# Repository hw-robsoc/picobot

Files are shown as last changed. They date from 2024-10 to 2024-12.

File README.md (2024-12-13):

# Welcome to the Robotics Society PicoBot Pico code

This repo contains the printable files for the Picobot, alongside the basic MicroPython code, which for Bluetooth control of the Pico's output pins, when connected correctly to the motor controller and servo. 

# Files

| |Description										|
|---|---|
|[main.py](https://github.com/hw-robsoc/picobot/blob/main/main.py "main.py")		|Main controller program, runs after boot of the Pico.|
|[test_motors.py](https://github.com/hw-robsoc/picobot/blob/main/test_motors.py "test_motors.py")|Test program to check that the directions of the motors are set correctly. |
|[test_servo.py](https://github.com/hw-robsoc/picobot/blob/main/test_servo.py "test_servo.py")|Test program to check that the directions of the servo are set correctly.|
|[RPI_PICO_W-20240602-v1.23.0.uf2](https://github.com/hw-robsoc/picobot/blob/main/RPI_PICO_W-20240602-v1.23.0.uf2 "RPI_PICO_W-20240602-v1.23.0.uf2")|The MicroPico firmware version we are using, which includes access to newer BLE libraries.|
|[PicoBot-AllDriveTypes.pdf](https://github.com/hw-robsoc/picobot/blob/main/PicoBot-AllDriveTypes.pdf "PicoBot-AllDriveTypes.pdf")|The laser cut design for all laser cut parts. Note: This is provided as a PDF, as when exporting to SVG from illustrator, the dimensions are wrong, and when exporting to DXF, the order of cuts is changed, resulting in parts that don't break away from the acrylic sheet.|
|[PicoBot-DrifterWheel.stl](https://github.com/hw-robsoc/picobot/blob/main/PicoBot-DrifterWheel.stl "PicoBot-DrifterWheel.stl")| 3D printable wheels for the drifer type kart.|
|[PicoBot-Pivot-Mount.stl](https://github.com/hw-robsoc/picobot/blob/main/PicoBot-Pivot-Mount.stl "PicoBot-Pivot-Mount.stl")| Sample pivot mount design for the racer type kart.|
|[Instructions-Session1.pdf](https://github.com/hw-robsoc/picobot/blob/main/Instructions-Session1.pdf "Instructions-Session1.pdf") [Instructions-Session2.pdf](https://github.com/hw-robsoc/picobot/blob/main/Instructions-Session2.pdf "Instructions-Session2.pdf") [Instructions-Session3.pdf](https://github.com/hw-robsoc/picobot/blob/main/Instructions-Session3.pdf "Instructions-Session3.pdf") [Instructions-Session4.pdf](https://github.com/hw-robsoc/picobot/blob/main/Instructions-Session4.pdf "Instructions-Session4.pdf")| Instruction sets for assembly, wiring, programming, and power system!|

# Flashing firmware to the Pico
Hold down the BOOTSEL button while plugging the board into USB. The uf2 file below should then be copied to the USB mass storage device that appears. Once programming of the new firmware is complete the device will automatically reset and be ready for use.
More information: https://micropython.org/download/RPI_PICO_W/

# Programming the Pico
We use [Visual Studio Code](https://code.visualstudio.com/) to program the Picos, along with the [MicroPico extension](https://marketplace.visualstudio.com/items?itemName=paulober.pico-w-go). Be sure to check the requirements of the extension, especially the requirements for a Python 3.10 or newer version to be installed on your PATH or equivalent.

Clone the repo to a projects folder, or download it via the green box above. Then, open the folder with VS code. If the MicroPico extension is already installed, it should automatically check your COM ports for a suitable device. When the device is plugged in, it will add a "Pico Connected" to your Status Bar, and give a notification that a connection has been made to the Pico. To upload your code to the Pico, press `CTRL` + `SHIFT` + `P`, or Mac/Linux equivalent, and search for `MicroPico: Upload project to Pico`. Select this option with `ENTER`, and wait for the code to be successfully uploaded to the device. 
For more information on how to use the MicroPico extension, see the [Marketplace Page](https://marketplace.visualstudio.com/items?itemName=paulober.pico-w-go).

# Brief code explanation
While some basic comments are included in the code, an overview can be found below:

- The [aioble](https://github.com/micropython/micropython-lib/blob/master/micropython/bluetooth/aioble/README.md) library is used to handle bluetooth connections, specifically Bluetooth Low Energy (BLE) connections. When combined with the tasks below, it is able to advertise, and receive payloads from other devices (your mobile phone running the Android app).
- The [asyncio](https://docs.micropython.org/en/latest/library/asyncio.html) library is used, which implements a subset of the standard CPython asyncio library. Three tasks are created to run concurrently in coroutines. These three tasks are:
	- **Blink Task** - This task simply checks whether a Bluetooth device is connected, and if it is, blinks the onboard Pico LED once every second. Otherwise, it blinks once every 1/4 second.
	- **Peripheral Task** - This task advertises the services and characteristics over BLE, and waits for a device to connect.
	- **Sensor Task** - This task waits for the chosen characteristic to be written to, and sets the motor control/servo control as required.
- There are then three additional functions.  `control_motors` processes the angle and strength of the joystick input, and converts that to motor speed and servo angle values. `set_motor_speeds` directly modifies the PWM output of each of the pins, according to the values calculated in the `control_motors` function. `set_servo_angle` directly sets the PWM output for the servo control, as per the value calculated again in the `control_motors` function.

## Batteries:  

Unfortunately due to the risk assessments we have, we are unable to give out the Li-ion batteries that were used to power the karts. However, if you are wishing to continue running/changing the kart over time, then you are more than welcome to buy your own batteries, but please be safe!

The exact cell that the society has are: Samsung 25R - 18650 Battery - 2500mAh - 20A, purchased from [CellSupply.co.uk](https://www.cellsupply.co.uk/samsung-25r-18650-battery). You do **not** need to get the exact cell, however having some of the same characteristics is key. I'll outline some of the characteristics below, then link to places to purchase them.

-   It should be an "18650" cell, which is simply the size of the cell (18mm diameter, by 65mm length) to fit in the holders on the karts.
-   It ideally should have a nominal capacity of around 2500mAh or higher.
-   It should have a nominal voltage of 3.6V (or 3.7V). The batteries we use are specifically INR chemistry, learn more about chemistry types [here](https://www.ufinebattery.com/blog/what-is-the-difference-between-imr-icr-inr-and-ifr-18650-battery/).
-   It should have a discharge rate of over 10A. The ones we use are 20A.

### Storage

Batteries themselves, when sitting at a sensible voltage (not too near either end of the extremes), and not fluctuating in temperature, are relatively safe. The main concern when storing them is to avoid shorting them against themselves or other batteries. This can be done using a case like the ones we had in the lab, or something like [this from Amazon](https://www.amazon.co.uk/JJC-Water-resistant-Batteries-Organizer-Carrying/dp/B08H511CPF).

### Charging

We handled charging the batteries between sessions using our own battery chargers, however, they can be charged using the BMS that is built into your robots. **Always monitor batteries when they are charging, never leave them unattended!**

Charging through a specific charger builds good practice for removing the batteries from the robot and storing them safely. Nu Batteries, as mentioned below, sells chargers suitable for Lithium Ion cells [here](https://www.nubattery.co.uk/chargers).

If you do wish to charge the robot through the integrated BMS, you will need to attach an input source to the P+ and P- pads on the back of the BMS. RobSoc has a number of USB-C charging ends that can do this, please reach out to us via email/discord if you want to do this, and I'll produce some instructions and tips! Otherwise, the BMS we use is listed in the instructions set on our [github](https://github.com/hw-robsoc/picobot).

### Buying

Like mentioned above, we bought ours in bulk from CellSupply, however, they can be bought from many sources. Buying them via Amazon for example will cost a large amount, and the quality/brand may be unknown or generic brands. Buying brands such as Samsung/Sony/Panasonic gives a little bit more piece of mind.

Alternatively, they can be bought in Vape shops, as the 18650 cells are often used in rechargeable vapes. You can usually get decent quality batteries in decent quality shops. None of our committee vape, however if you have a friend that does, asking them if they have bought batteries for their vape may be a good starting point to find a good quality shop.

We can only recommend CellSupply as we bought ours through them. They are however a wholeseller. They do have a sister site, Nu Battery, where you can buy the exact same cells in much lower qualities for a not too bad price increase. [Here is the same cells we use from NuBatteries](https://www.nubattery.co.uk/samsung-25r-18650-battery).

### Alternative chemistries:

I mentioned during the event that there may be alternative battery chemistries such as NiMH (nickle metal hydride) batteries, however I didn't know the nominal voltage off the top of my head. These batteries are safer, however, they have a nominal voltage of 1.2V, which means you would need a minimum of 4 of them vs the 2 we currently use. On the up side, that would possibly negate the need for the voltage converter (if you don't charge the cells fully). Without a redesign of the BMS/Voltage converter, you would **not** be able to directly swap in a NiMH battery, however if you are interested in doing this, please post on the Discord server, and we can try to figure it out!

## Finally, if you have any doubt, please send a message on our discord, and one of the committee would be more than happy to advise! Batteries when handled safely are a great resource!

# Licence

MIT License

Copyright (c) 2024 Bruce Wilson

Permission is hereby granted, free of charge, to any person obtaining a copy
of this software and associated documentation files (the "Software"), to deal
in the Software without restriction, including without limitation the rights
to use, copy, modify, merge, publish, distribute, sublicense, and/or sell
copies of the Software, and to permit persons to whom the Software is
furnished to do so, subject to the following conditions:

The above copyright notice and this permission notice shall be included in all
copies or substantial portions of the Software.

THE SOFTWARE IS PROVIDED "AS IS", WITHOUT WARRANTY OF ANY KIND, EXPRESS OR
IMPLIED, INCLUDING BUT NOT LIMITED TO THE WARRANTIES OF MERCHANTABILITY,
FITNESS FOR A PARTICULAR PURPOSE AND NONINFRINGEMENT. IN NO EVENT SHALL THE
AUTHORS OR COPYRIGHT HOLDERS BE LIABLE FOR ANY CLAIM, DAMAGES OR OTHER
LIABILITY, WHETHER IN AN ACTION OF CONTRACT, TORT OR OTHERWISE, ARISING FROM,
OUT OF OR IN CONNECTION WITH THE SOFTWARE OR THE USE OR OTHER DEALINGS IN THE
SOFTWARE.

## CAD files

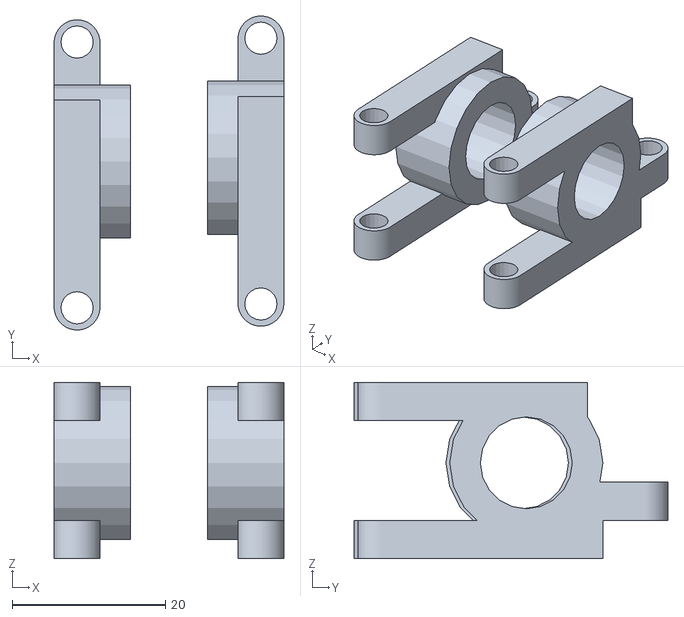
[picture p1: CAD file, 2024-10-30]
PicoBot-Pivot-Mount.stl
30.0 x 41.0 x 23.0

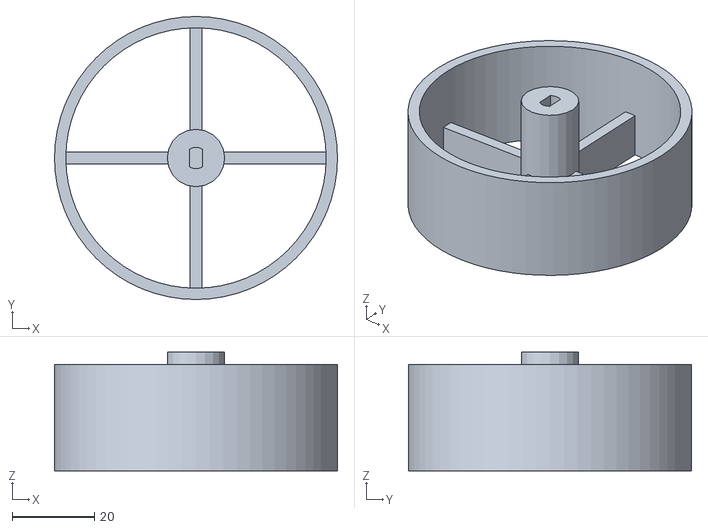
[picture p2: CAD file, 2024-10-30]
PicoBot-DrifterWheel.stl
69.0 x 69.0 x 29.0

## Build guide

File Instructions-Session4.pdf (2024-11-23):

# Robotics Society – Kart Workshop

### Session 4 – Power pack

Last week, we wired up and programmed the Pico for control from the Android app. This week, we will build and solder the power system, which works using a 2S Li-ion battery, with an attached BMS and step-down voltage converter. Both kart designs use the same power pack. Note: Lithium-Ion cells have very high power and energy density. Exercise common sense

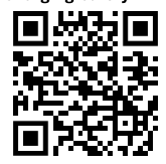
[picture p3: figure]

precautions when handling or testing.

# Part list

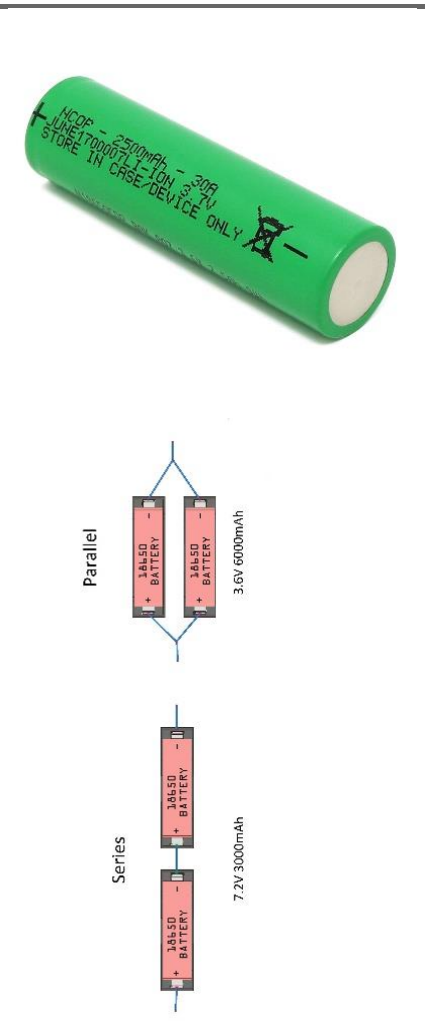
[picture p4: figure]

Part name | Description/use | Picture
Li-ion Battery Cell 18650 - 3.6V 2500mAh - 20A Information about Li-ion charging/safety: | We use these 2500mAh lithium ion cells to provide power to the system. Each cell nominally provides 3.6V, however, they can vary from 4.2V to 2.5V depending on their charge level. It is incredibly important to monitor their charge level, as keeping the voltage near either end of the range for a period of time can cause irreversible damage. Realistically, the voltage should never be allowed to drop below 3V. Even more dangerous is going past the end of this maximum/minimum, which can cause a fire or worse. Due to the variability of the voltage, firstly, a regulator is important to supply a constant voltage across the system. Secondly, a monitoring system is needed to keep within the range, as the batteries themselves do not monitor any of these factors.
| We will use two of these cells in series, and when batteries are placed in series, their voltage is added. Thus, we will have a nominal voltage of 7.2V, maximum of 8.4V, and minimum of 5V.

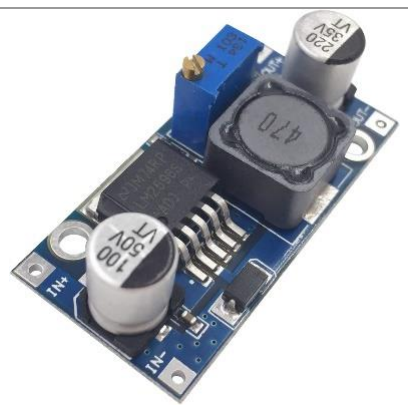
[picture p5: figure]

LM2596 DC to DC
Buck Converter

More about buck
converters:

As our nominal, minimum, and maximum vary significantly, we need to use a voltage regulator. If you remember from Session 2, the maximum voltage the RPi Pico can handle is around 5.5V.
We can use a step down buck converter to keep this voltage constant, around 5.2V. There are four solder pads on this board, two input, and two output, labelled by IN and OUT, and marked with a direction arrow on the back of the board.
We can adjust the voltage output by taking a screwdriver and turning the brass screw in the blue variable resistor. Test the output by attaching a voltmeter to the OUT pins, and vary the position of the brass screw to see its output.
2S 3A Li-ion Battery
Charger Protection
BMS

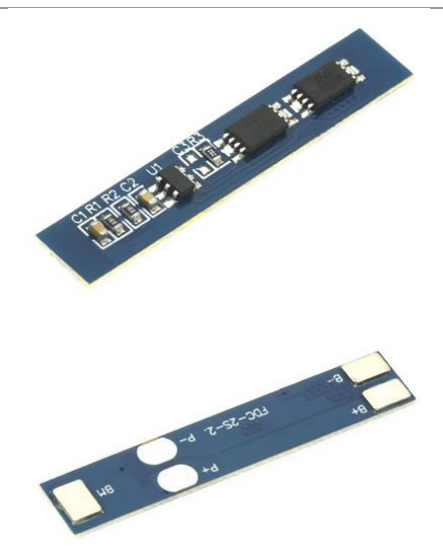
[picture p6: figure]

As mentioned above, ensuring that the li-ion battery is not over-discharged, over-charged, or too much current is drawn from the battery, we use a BMS, which stands for Battery Management System. This small chip takes three input, B+, B-, and BM. B+ and B- are simply the positive and negative input from the battery itself. BM however connects to the midpoint between the two batteries, which ensures that both batteries are charged at the same rate, and individual cells can have their voltage measured. P+ and P- are then multiuse pins, acting both as charging pads and discharging pads. For our basic use, we will connect the P+ and P- pads to just discharge, and charge the batteries using a Li-ion charger. However, USB-C connectors are available to solder on if desired.

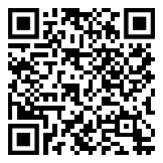
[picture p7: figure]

# Wiring Diagram and Description

Ideally, the cells would be contained within a small housing, with the BMS and voltage regulator attached to the outside, however, as we are placing the cells into a cell holder anyway, the outside of this can be used to attach the components to.

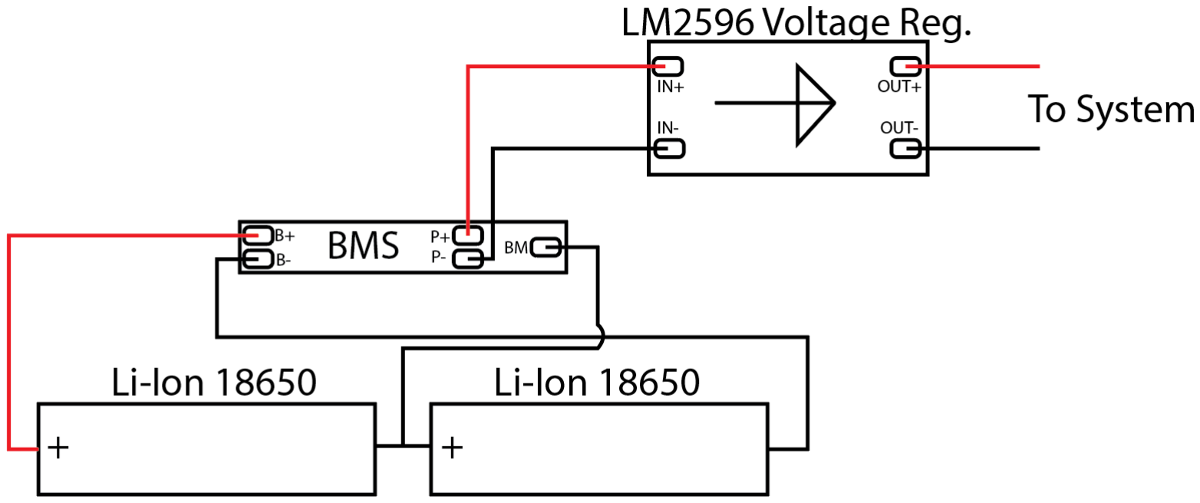
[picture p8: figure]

The diagram above demonstrates the principles covered in the part list in action. The BMS can be mounted to the side of the battery holder, where as the voltage regulator can be mounted atop the batteries themselves with a piece of tape.
Key to this part of the project will be soldering. DO NOT solder directly to a li-ion battery, it is highly dangerous, and even the prolonged high temperature can damage the cells. In this workshop, we are using a 2x18650 plastic holder, however in practice, many cells are joined together using spot welding and nickel plating.
A few notes to take into account, the pads on the BMS like to move about when the solder flows, so a steady hand is needed to keep them in place, and leave them to cool once in position. Additionally, soldering the connector piece for the BM lead is tricky, and has to be soldered onto a connector on the battery pack itself.
In the session, we will take small groups over to solder these together, but outside these sessions, please do let us know if any help is required.
Please note, we require the cells back at the end of the session, or for them to be stored securely between sessions. Leaving exposed cells around can be dangerous, especially if someone without the knowledge of the cells starts handling them.

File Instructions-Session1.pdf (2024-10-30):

# Robotics Society – Kart Workshop

### Session 1 – Assembly

Welcome to the Robotics Society Kart Workshop! Over the
course of 3-4 weeks, you will be assembling, wiring up, soldering, and powering your very own kart, which can drive around our track, and compete in our competition on November 20th

,
hosted in the National Robotarium!
These instructions are intended to be followed alongside the
practical workshop, with RobSoc committee guiding you through
each instruction – however they are also produced for those who

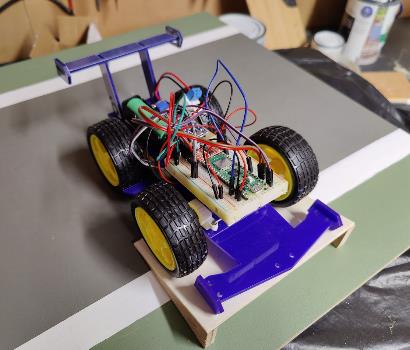
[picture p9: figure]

cannot make the sessions, or want to catch up. Please let us know if anything is not clear! Following the instructions throughout the sessions will get you a working kart – however it will not be the best you can make! The general kart we designed was built for ease of manufacturing and simplicity, at the cost of speed and control. Thus, it is up to you to make changes and make your kart the fastest round our course!

# Your choices – Racer or Drifter

First, there are two base designs for the kart, the “racer” and the “drifter”, with subtle changes to the assembly and wiring depending on which design you choose. The racer style makes use of four rubber wheels, rear-wheel drive with two motors, and a servo at the to pivot the front wheels to steer. The drifter style makes use of differential trust steering on the front two rubber wheels, and free spinning 3d printed wheels at the rear to reduce friction.
Both kart designs use the same laser cut components, and a majority of the holes and mounting points on the laser cut parts are not used, but are there for mounting any powerups you wish to add, or modifying your kart design without using the laser cutter.

# Assembly Steps

We’ll start with basic assembly which applies to both karts, then break off into specific assembly relevant to each kart design.
A huge note: Our budget is tight, especially with us not charging membership this year. Cheap acrylic was bought, which has quite a large variation of depth across its surface. Thus, parts can be tighter/looser than intended in the design. A sheet of sandpaper and a needle file can go a huge way, and parts such as the vertical connectors or spoiler are prone to breakage. Don’t worry if a part snaps! We have made many spares to account for the variation.
Additionally, various inserts may be stuck inside other pieces – just give them a gentle push with a fingernail or tool and they should pop out.

## Laser Cut Parts

The below kit will be provided, with other parts – not including electronics – are provided either through the society box or the GRID tower (for bolts and wires). See the other parts list below for a full description

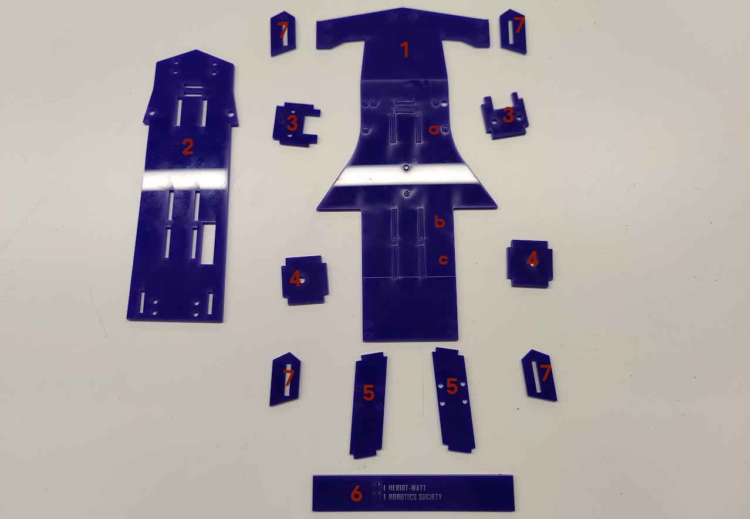
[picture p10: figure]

## Additional Part List

Racer | Drifter
- 4x rubber yellow wheels • 1x sg90 micro servo • 1x half servo horn with 3mm hole drilled at 3rd up • 2x yellow motor (double shaft) with crimped connectors • 2x 3d printed pivot wheel mounts • 2x 12mm 4mm bore shaft bearings • 4x 4mm shaft collars • 2x 4mm 26mm aluminium axle • 1x 2mm steel wire control linkage • 2x M4*16mm bolts (with 4x M4 nuts) • 4x M3*25mm bolts (with 4x M3 nuts) • 1x breadboard | • 2x rubber yellow wheels • 2x 3d printed wheels • 1x 4mm 83mm aluminium axle • 2x yellow motor (double shaft) with crimped connectors • 4x M3*25mm bolts (with 4x M3 nuts) • 2x 4mm shaft collar • 1x breadboard

## Part Descriptions (for reference)

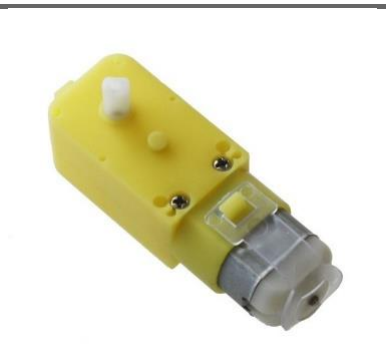
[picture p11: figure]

Part Name | Description/use | Picture
Yellow Motor with crimped connectors | These motors are relatively slow, but with the gearbox addon can produce a reasonable amount of torque. Expect around 90RPM from their output, when given nominal voltage of 4.5V (operating range of 3V to 6V). Motors rotate when a voltage is applied across them, and while modifying their speed via adjusting the voltage is possible, it is far better to modify their speed using PWM signals, and we go a step further by using a motor controller, which will be explained in session 2.

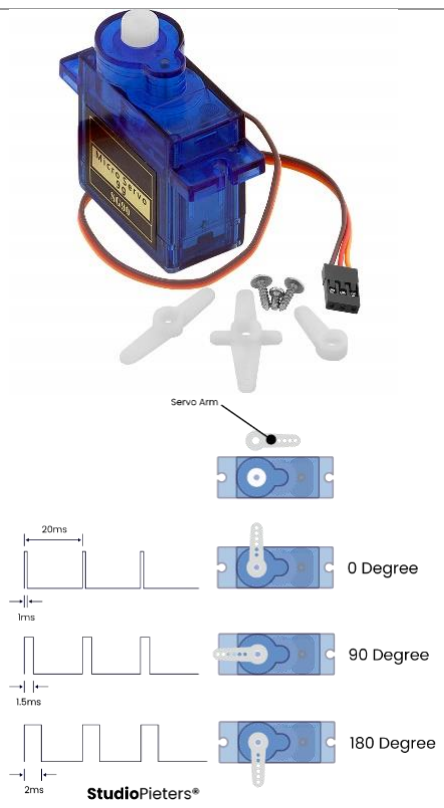
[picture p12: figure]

SG90 Micro
Servo / Half
servo horn

Learn more
about servos
and PWM:

Servos require both a supply through their red and brown wires, but also a signal through the yellow wire. This signal is a PWM signal, which stands for Pulse Width Modulation. By applying short pulses of voltage in a specified pattern, the servo can be made to rotate to and hold a certain angle, which in our case, is between 0 and 180 degrees. In the example to the right, it is shown how adjusting the length of the pulse while keeping signal frequency (50 Hz) the same, can rotate the servo between 0 and 180 degrees.
The servo horn is the small piece of plastic that attaches to the end of the gear train, and can attach to your control linkage to pivot the wheels at the front of the racer kart. This piece is incredibly easy to snap – which is beneficial if the servo tries to rotate too quickly, and you’d rather the horn snapped than the servo broke itself.
The SG90’s that we are using can safely handle up to about 5.3V, and will probably not rotate with anything under 3.3V. Servos can be current hungry when they rotate quickly and with load, easily spiking to 2A. This is the reason a 2S system with step down voltage will be used for the power system.

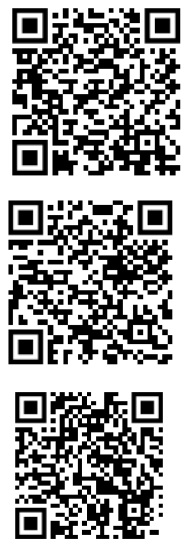
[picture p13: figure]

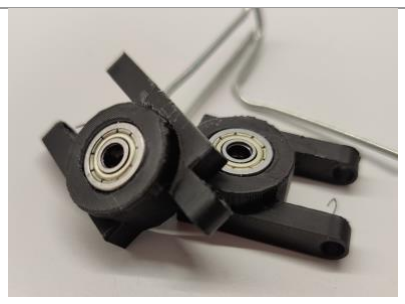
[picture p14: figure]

3D printed Pivot wheel mounts | These parts are designed to hold a bearing, and connect to both the top and bottom assembly of your kart. They are not optimal, as they rotate about 20mm off the axle connection point. An improvement to your robot could easily be designing a 3D printed piece that connects directly below the axle connection point (hint: there is a pre-made hole in part 1 where this could go!)

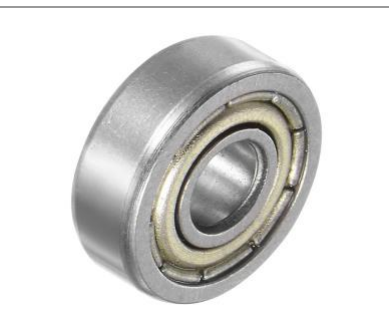
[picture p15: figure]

Shaft bearings | These bearings allow for the front wheels of the racer type kart to rotate easily and with less friction. They have an external diameter of 12mm, and an internal bore of 4mm, which fits the aluminium axle. Hint: These could be used on the drifter type cart to allow both rear wheels to spin independently, which would reduce friction further, rather than having both rear wheels mounted on the same axle.

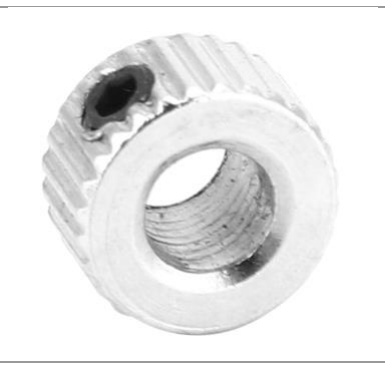
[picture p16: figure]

Shaft collars | Shaft collars prevent the axle from slipping around, and are tightened using an M3 grub screw. The inner bore of the shaft is 4.1mm.
Aluminium Axle | The drifter kart design uses a single axle at the rear connecting both wheels together, using shaft collars to prevent slippage. The racer kart design uses two axles at the front to connect the wheels to the bearing mounted inside the pivot wheel mount. The aluminium is 4mm round bar, which is relatively easy to bend or grind, with all squared ends done using a bench sander.

## Step 1

Start by assembling the spoiler and top assembly to get an idea of how the parts fit together, and how much sanding is needed. Part 5 (spoiler bars) will slot into part 6 (spoiler), such that the logo is facing up, and the spoiler bars are both heading the same direction. Both part 5’s should then assemble together into part 2 (top plate), and form the image you can see on the right. Part 7 can be added as
desired to the sides of the spoiler.

## Step 2

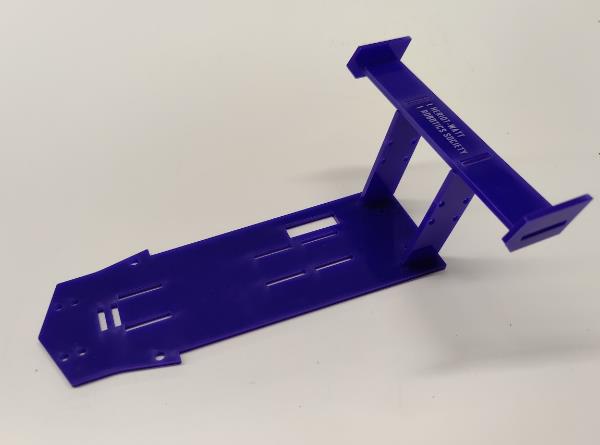
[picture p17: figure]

Each yellow motor should be connected to part 3, with the mouth of the space invader facing towards the silver end of the motor, and with the copper solder points of the motor facing towards part 3 as shown. Two 25mm M3 bolts should be inserted through the motor and through part 3, and two M3 nuts placed on the end to hold the piece together, as shown on the right.

## Step 3

Depending on the kit you receive, you may receive motors

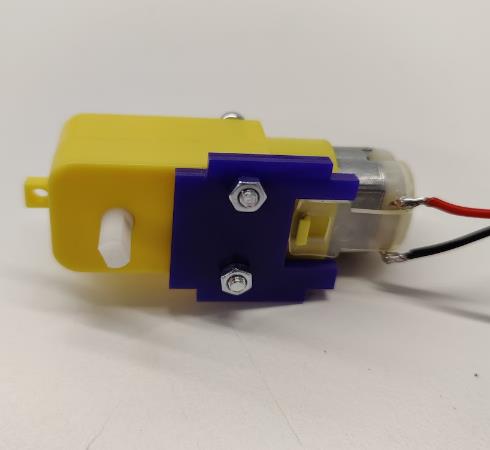
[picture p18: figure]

with pre-soldered connectors, or just copper tabs on the end of the motors. If you have never soldered before, please come along to one of our sessions, and we can teach the basics of how to solder onto these tabs. If you know how to solder already, feel free to solder wires of around 15cm length onto these tabs, multicore, with a max AWG of 16 (to enable easier crimping). Once the motor wires are soldered, 2x1 crimps should be added to the end, to aid with connection to the breadboard (RobSoc has crimping tools in the box, or, there should be a crimping tool and crimps per floor of GRID).

## Racer Steps

### Step 4

Insert the two motors mounted on part 3 in the rear straight holes of part 1 (labelled b in the diagram of laser cut parts). The end of the motors, with the yellow piece of plastic sticking out, should align with the engraved line on part 1, as shown to the right. Both part 4’s can then be inserted into the front straight holes on part 1 (labelled a in the diagram of laser cut parts). Once this bottom assembly is together, you can test fit whether the top assembly that you made in part one fits, or requires further sanding of parts 3 and 4. Then, attach two rubber wheels to the motors at the rear.

### Step 5

Two 3d printed pivot wheel mounts either in black or white will be included with the kit. Press fit one 12mm bearing into each pivot mount, with the bearing flush with the protruding section of the mount, as shown to
the right. Next, these mounts should be
attached to part 1 with a 16mm M4 bolt, with

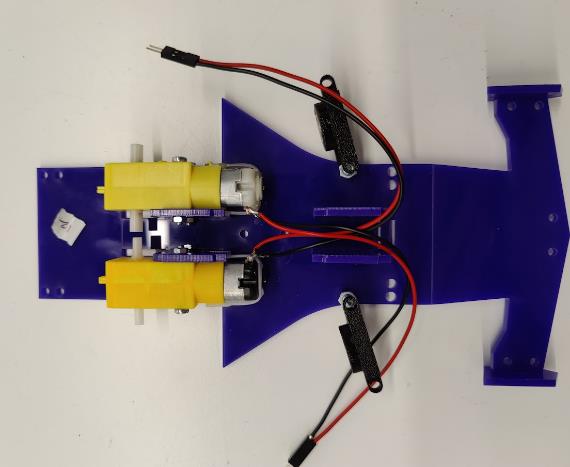
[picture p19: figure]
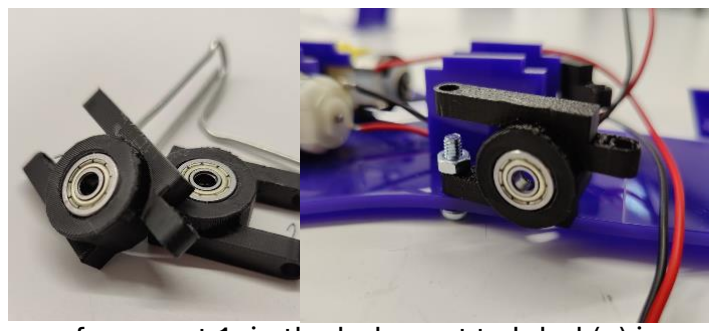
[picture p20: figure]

the protruding piece of the pivot mount facing away from part 1, in the hole next to label (a) in the laser cut parts diagram, and secured with a single M4 nut. Once you are happy with the positioning, a second M4 nut can be used to tighten the two nuts against one another, preventing vertical movement of the pivot mount, but allowing rotation.

## Step 6

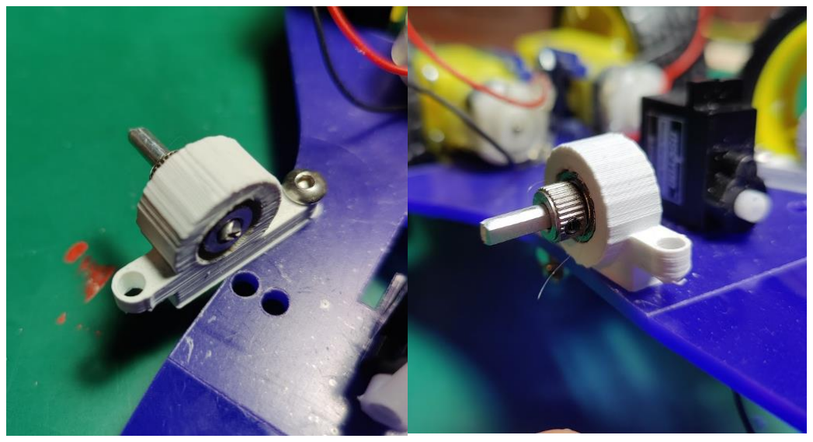
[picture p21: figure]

Position one 26mm
axle through each of
the bearings, such
that the chamfered
end is facing away
from part 1. On each
axle, place a shaft
collar either side of
the bearing, and
tighten the grub nuts
so that the axle
extends no further
past the end of the
shaft collar.

## Step 7

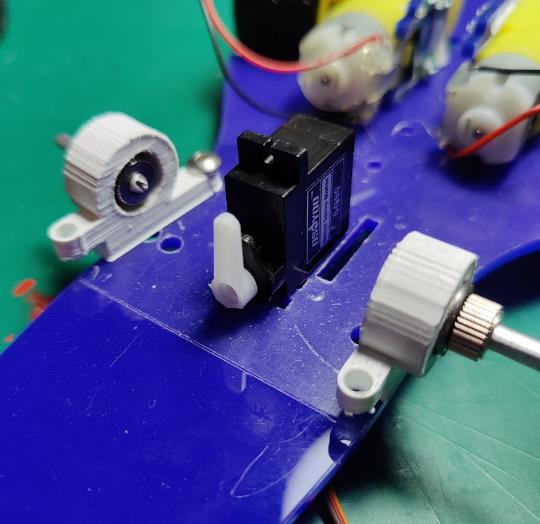
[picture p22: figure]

Mount the servo with the single armed horn (white piece that attaches to the rotating circle on the servo) in the centre straight holes of part 1. There are two position options, depending on how you design the control linkage in step 8, and we recommend the rear option. A key note: is that the servo may have been rotated prior to mounting, and you cannot guarantee that the position you put the horn will be the centre of the servo. Thus, always ensure in your design that you can remove the servo horn from the servo itself.

## Step 8

Connect the servo to either pivot rod ends using a control arm, made from steel wire. This design can take many forms, with benefits and drawbacks to each, and is a key point where upgrades can be made to the kart, for example, using multiple moving components to implement Ackerman steering. The example shown to the right creates a relatively large turning circle, and by changing the attachment point on the servo horn, a smaller circle is possible, by
increasing the pivot range.
Some additional details: You want the wire to be

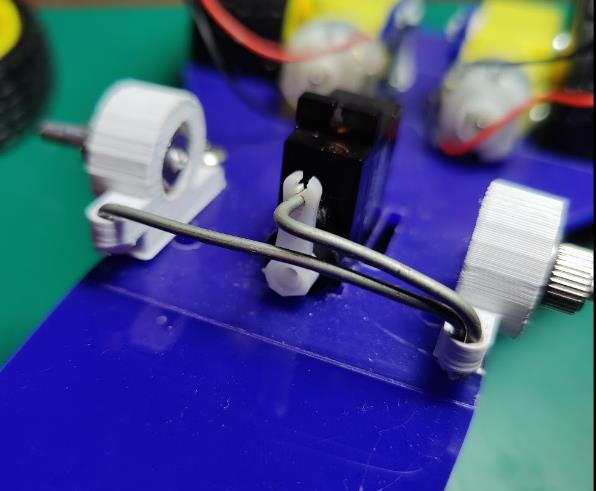
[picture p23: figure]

able to rotate within each of the pivot rod ends, and rotate within the servo horn itself. The servo horn will also need drilled out to 2mm if using the steel wire supplied, which is best done very slowly, and using just friction and a bit of force, though, don’t worry if it snaps at the end, this is usually okay, unless it snaps closer to the horn connector.

## Step 9

Attach the top assembly onto the bottom assembly, and mount two rubber wheels onto the ends of the 26mm axles. If they are loose, they can be secured by hot gluing a small blob onto the wheel hole, then inserting the axle and letting the glue set. Attach part 7 to the front of part 1 and sides of part 6 as desired, then assembly of the racer type kart is complete! Next steps are beginning wiring and electronics, covered in session 2.

## Drifter Steps

### Step 4

Insert the two motors mounted on part 3 in the front two straight holes of part 1 (labelled a in the diagram of laser cut parts). The end of the motors, with the yellow piece of plastic sticking out, should aligned with the engraved line on part 1, as shown to the right. Both part 4’s can then be inserted into the rear straight holes on part 1 (labelled c in the diagram of laser cut parts). These should be inserted with the centre hole higher, otherwise the kart will be unbalanced. Once this bottom assembly is together, you can test fit whether the top assembly that you made in part one fits, or requires further sanding of parts 3 and 4.

### Step 5

Insert the supplied 4mm*84mm axle through the two holes in part 4. Then center and secure it using two 4mm bore shaft collars, by tightening the black grub screws in the collar. Then, attach the two 3d printed wheels to the ends of the axle. If they are loose, they can be secured by hot gluing a small blob onto the wheel hole, then inserting the axle and letting the glue set.

## Step 6

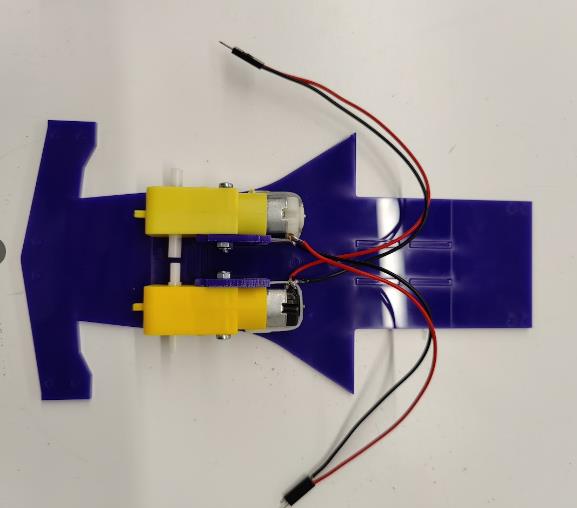
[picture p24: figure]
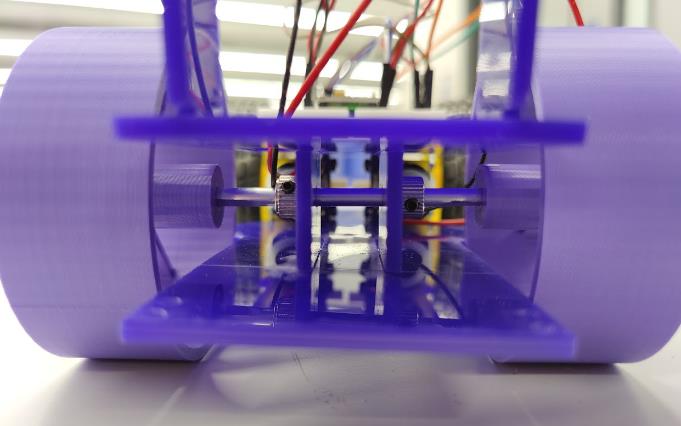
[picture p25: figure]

Attach the supplied rubber wheels to the motors at the front of your kart, and part 7 to the front of part 1 and sides of part 6 as desired, then assembly of the drifter type kart is complete! Next steps are beginning wiring and electronics, covered in session 2.

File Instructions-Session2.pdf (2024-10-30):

# Robotics Society – Kart Workshop

### Session 2 – Electronics

Last week, you began assembly of the karts, putting together the laser cut frame and beginning the wheel assemblies depending on your design. Today we will be completing the initial electronics setup, wiring up the Raspberry Pi Pico, DRV8833 motor controller, and depending on your choice of kart, the wheels or servo. We don’t include a direct wiring diagram in here – that’d be too easy! But you can compare against the working kart in the sessions.

# Part list

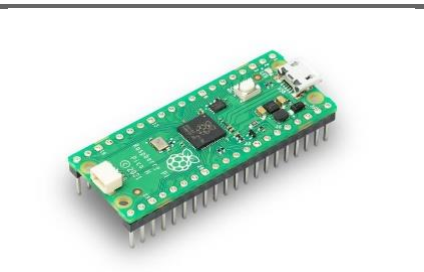
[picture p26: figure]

Part name | Description/use | Picture
Raspberry Pi Pico W Documentation: | The main controller for the system, receiving input from its onboard Bluetooth chip, processing the input signals, and outputting appropriate PWM signals to the motor controller. The Pico itself can handle an input voltage of up to around 5.5V, though we recommend keeping it slightly below this. The whole board can be programmed in multiple languages, for our workshop we will be using MicroPython. Though it can be programmed directly in C, the software that interfaces with the Bluetooth capabilities is much more complex in C than Micropython.

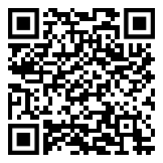
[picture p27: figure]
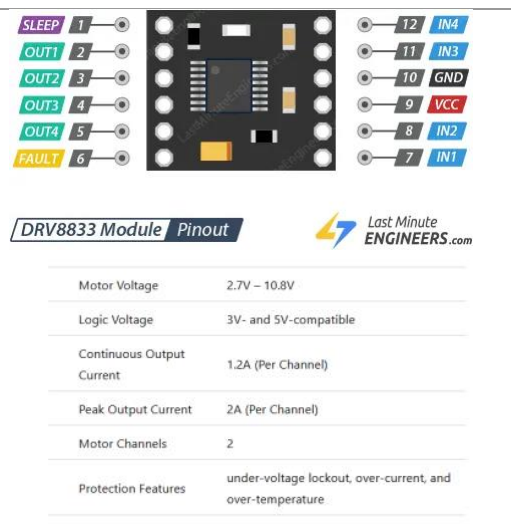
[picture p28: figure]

DRV8833 Motor Controller Documentation: | This board receives the PWM signals from the Pico and controls the motor forward and backwards at varying speeds. Using a motor controller is important, as the Pico is not designed to control motors nor servos directly off its internal voltage regulator. Motors and servos can draw large currents quickly, for example while changing directions. They can also produce back EMF, which the Pico will not be expecting or able to handle without additional components. The motor controller solves these problems and combines the solution into a single board

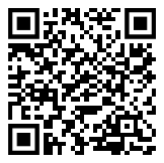
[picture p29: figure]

# Wiring Description

To control the motors effectively, we need to supply the motor controller with 4 possible PWM signals. PWM is effectively turning a signal on and off very fast, and with this switching, the time that the device is on will stabilise to an overall lower voltage. For more information and answers to “why cant we just directly turn the voltage down”, see here:

In our sample program, we output this from GP0-3. It should be noted, that when using PWM signals from the Pico, care must be taken to avoid trying to set different frequencies on the same channel. The Pico has 8 independent PWM generators called slices. Each slice has two channels (A and B), which makes a total of 16 PWM channels. While different outputs can be sent to each channel, the frequency is set per slice. This is only important for us, as the PWM frequency for the motors versus the servo will be different. More information is available in the Pico documentation, linked at the top of this document.
Our motor controller makes use of the dual h-bridge driver, the DRV8833, and can handle up to a maximum of 10.8V. The DRV8833 also contains several protection features, such as under-voltage lockout, over-current, and over-temperature protection. Each of these events will disable the device, and will only resume its operation after the fault has been removed. To learn more about the H-bridge drivers and motor controller work internally, see the documentation linked in the table above.
The board itself is made up of 12 pins, with 4 dedicated to input PWM signals, 4 dedicated to output motor control, and 2 for power input (Note: This motor controller uses the same motor and logic voltage, thus only one power supply for the whole unit is required). Additional pins are not used in our use case, but are described in the docs above.
Four input pins on the controller receive the 4 PWM signals that we generate above from the Pico. These control both the speed and direction of the motor. A table below shows how changing the levels of these input pins controls the motor: (Note: One motor is controlled using IN1 & IN2, and the other motor controlled by IN3 & IN4).

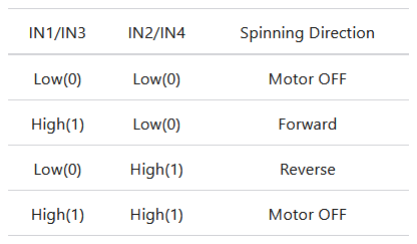
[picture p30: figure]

## Step 1

Press the Pico into the breadboard, with pins 1 and 40 touching one end of the board. Verify this by ensuring the MicroUSB connector is at the edge of one of the breadboards. Breadboards are connected in lines both horizontally and vertically. See the diagram below for examples of which pins are grouped together. Remember, you want each pin that the Pico presses into the breadboard to be on its own group (a green group), no two pins should be grouped together. The red and blue groups at either side of the breadboard are called “rails”, and they are used for power, with red corresponding to your positive voltage (~5V for us), and blue corresponding to 0V (or ground).

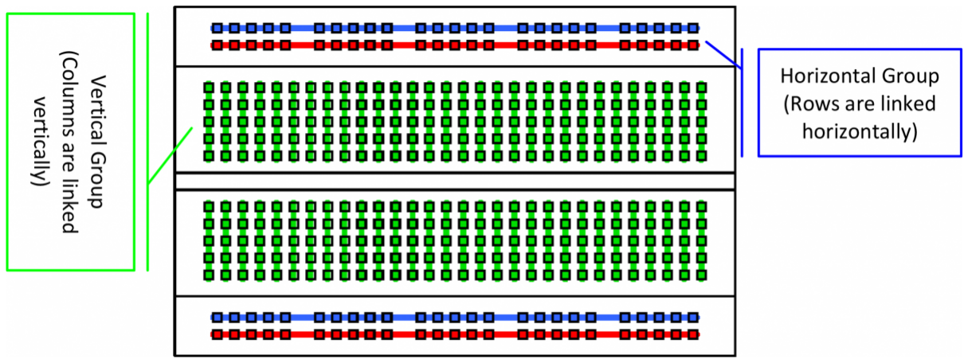
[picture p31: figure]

After the Pico is correctly placed into the breadboard, press the DRV8833 board into the available end of the breadboard. First, check the bottom of the motor controller, and see which side is labelled with the pins GND and VCC. Place these pins facing the same side as pin 40 of the Pico (remember, the pins on the DRV are on the bottom of the board, so try not to flip it around when placing it in!)

Connect the GP0-3 pins from the Pico in order to the IN1-4 pins on the motor controller, using jumper wires. If the wires are too long, don’t worry, we can find shorter wires later to improve the aesthetics. Verify each jumper connects as follows:
- GP0 – IN1
- GP1 – IN2
- GP2 – IN3
- GP3 – IN4

## Step 2

Connect the required 5v and ground pins to both the motor controller and Pico. These should come from your 5V and 0V rails running alongside your breadboard (however don’t worry this rail isn’t powered until we plug in our battery next week).
With the Pico, connect a jumper wire from pin 39 (VSYS) to the red 5V rail on the side of your breadboard; then from pin 38 (GND) to the blue rail on the side of the breadboard. Ensure you plug into VSYS, as this pin accepts an external system voltage in between 1.8V and 5.5V Similarly, connect pins VCC on the motor controller to the red 5V rail, and the GND pin to the 0V blue rail on the side of the breadboard.

## Step 3

Connect the motor wires that you crimped previously to the motor controller. These pins are the center 4 on the side of the motor controller that you haven’t used yet. Ensure that one motor is connected to pins OUT1 & OUT2, then the other motor to OUT3 & OUT4. Which pins are plugged into which OUT between 1&2 doesn’t matter yet, we will likely have to adjust it later.

## Step 4 (racer karts only with servo)

Jumper wires or recrimping the servo wires to male ends can be chosen to connect the servo lead end to the breadboard. We would recommend just using long jumper wires for now, and then recrimping in time.
The servo has three input wires: red for positive voltage, black for ground (0V), and orange for signal.
Plug the red and black wires directly into the red and blue rails on your breadboard, corresponding red to red and blue to black.
Plug the orange signal wire into GP6 on the Pico connectors. This can be adjusted in the code, however for ease of some space on the breadboard, this was selected as the default. Finally, jump pins GP15 and 3v3V OUT between the Pico. This is to tell the program running on the Pico to use servo mode rather than differential motor control.

## Wiring complete

All wires apart from power supply should now be connected on your breadboard, and you can move onto programming the Pico!

# Pico Pinout:

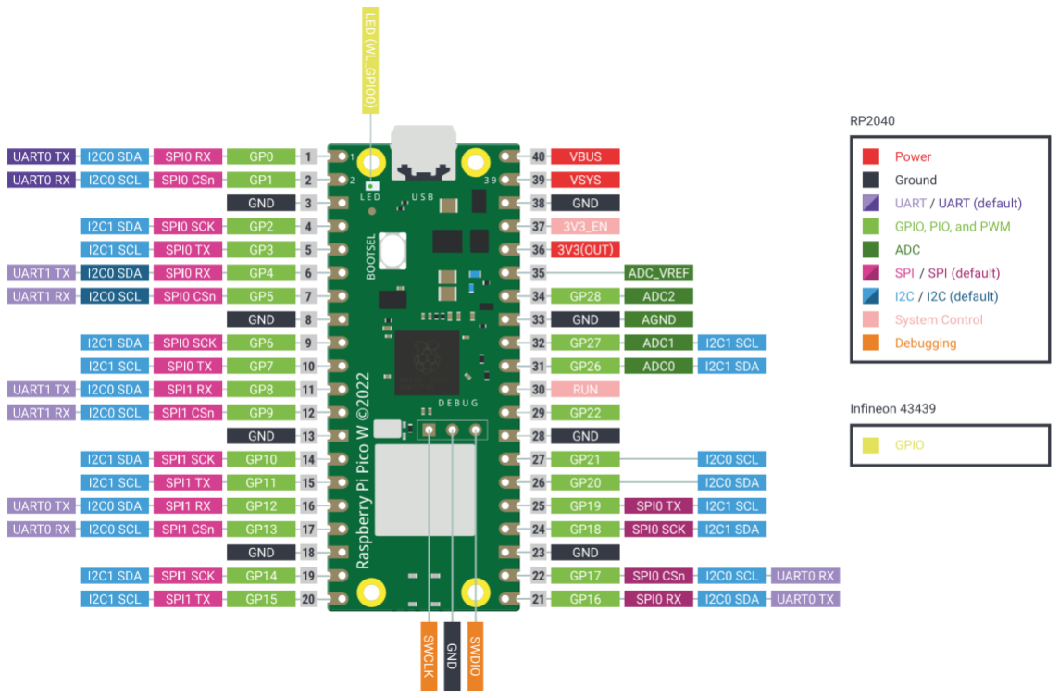
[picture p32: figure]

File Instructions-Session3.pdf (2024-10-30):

# Robotics Society – Kart Workshop

### Session 3 – Programming

Last week, we wired up the Pico to the motor controller and connected the motors/servo. This week, we will be looking at the Pico programming, and how we can do some basic testing of the system.
First as a note, all Picos we provide will come pre-programmed with the controller code, and flashed with the MicroPython firmware. They will have a sticker taped to the bottom, this is the name they are advertising when you search for them in the PicoBot app.
MicroPico and Design files | PicoBot Bluetooth Android App

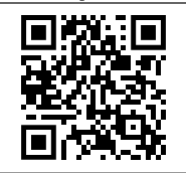
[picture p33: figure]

# Flashing firmware to the Pico

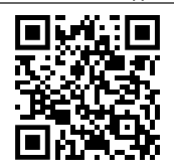
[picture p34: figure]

Hold down the BOOTSEL button while plugging the board into USB. The uf2 file below should then be copied to the USB mass storage device that appears. Once programming of the new firmware is complete the device will automatically reset and be ready for use. More information: https://micropython.org/download/RPI_PICO_W/

# Programming the Pico

We use Visual Studio Code (https://code.visualstudio.com/) to program the Picos, along with the MicroPico extension. (https://marketplace.visualstudio.com/items?itemName=paulober.pico-w-go) Be sure to check the requirements of the extension, especially the requirements for a Python 3.10 or newer version to be installed on your
PATH or equivalent.
Clone the repo to a projects folder, or download it via the green box above.
Then, open the folder with VS code. If the MicroPico extension is already installed, it should automatically check your COM ports for a suitable device. When the device is plugged in, it will add a "Pico Connected" to your Status Bar, and give a notification that a connection has been made to the Pico. To upload your code to the Pico, press CTRL + SHIFT + P, or Mac/Linux equivalent, and search for MicroPico: Upload project to Pico. Select this option with ENTER, and wait for the code to be successfully uploaded to the device.
Most importantly: Please keep the robot-X number the same as what is on the sticker on the bottom of your Pico! This will avoid multiple people ending up with the same advertising name.

# Brief code explanation

While some basic comments are included in the code, an overview can be found below:
- The aioble (https://github.com/micropython/micropython-lib/blob/master/micropython/bluetooth/aioble/README.md) library is used to handle bluetooth connections, specifically Bluetooth Low Energy (BLE) connections. When combined with the tasks below, it is able to advertise, and receive payloads from other devices (your mobile phone running the Android app).
- The asyncio (https://docs.micropython.org/en/latest/library/asyncio.html) library is used, which implements a subset of the standard CPython asyncio library. Three tasks are created to run concurrently in coroutines. These three tasks are:
- Blink Task - This task simply checks whether a Bluetooth device is connected, and if it is, blinks the onboard Pico LED once every second. Otherwise, it blinks once every 1/4 second.
- Peripheral Task - This task advertises the services and characteristics over BLE, and waits for a device to connect.
- Sensor Task - This task waits for the chosen characteristic to be written to, and sets the motor control/servo control as required.
- There are then three additional functions. control_motors processes the angle and strength of the joystick input, and converts that to motor speed and servo angle values. set_motor_speeds directly modifies the PWM output of each of the pins, according to the values calculated in the control_motors function. set_servo_angle directly sets the PWM output for the servo control, as per the value calculated again in the control_motors function.

# PicoBot Android app

The PicoBot Android app is created as a joystick controller, and is built in Android Studio, and based off the PunchThrough android BLE guide. A short list of the files of interest to you are listed below. Other files are used, but contain the meat of BLE connections, and are not necessary to read through unless you want a deeper understanding of how the BLE connection is handled. Android apps are made up of many file types, but the two most important are Kotlin files and xml resource files. The Kotlin programming language is similar to Java, in that it runs within the JVM, but provides a more modern and concise language that is being adopted by more software developers. Using AndroidStudio, which is based on JetBrains IntelliJ, code linting and autocomplete is available, which helps with early Android development.
We make use of the virtual-joystick-android library, and a few other dependencies, to simplify the implementation.

File name | Description
MainActivity | Android apps are at their code made up of screens, called activities. Context, coroutines, and much more can be scoped to be available only to a specific activity. Diving in deeper, multiple fragments can be displayed within a single activity, but that is outwidth the scope of this session. The MainActivity class in our app begins by requesting permissions if they have not already been requested, and sets up the scanning button, and recycler view (scrollable list that is resource efficient). When the Start Scan button is clicked, the app uses other classes to search for nearby advertising BLE devices.
ConnectionManager | Handles establishing, processing, and writing/reading communication from a BLE device.
RobotControlActivity | Creates and queues connections to be sent using the ConnectionManager to the Pico. Reads and parses the joystick input, and has TODO blocks where the special toggles can be implemented.
activity_robot_control.xml | An Android resource file, which creates the visual layout for the interface. It includes the joystick, logo, and special move buttons.

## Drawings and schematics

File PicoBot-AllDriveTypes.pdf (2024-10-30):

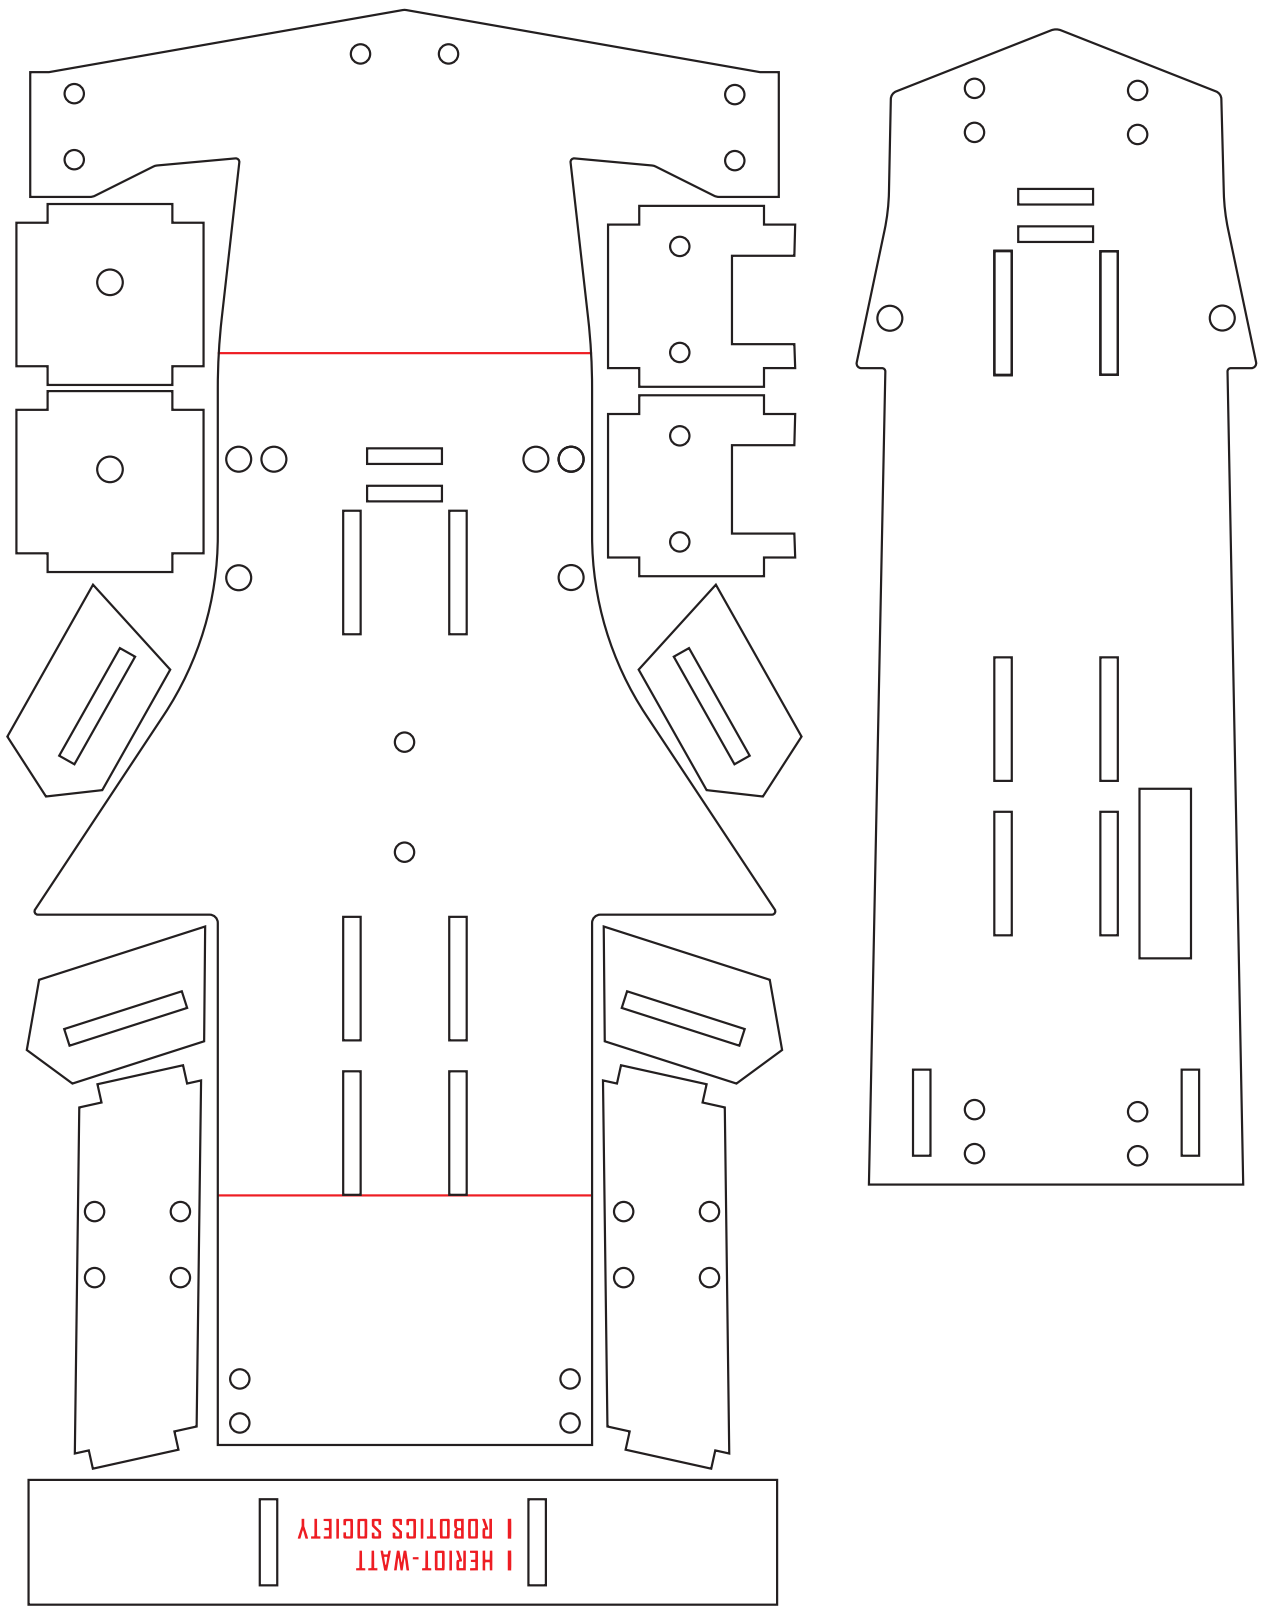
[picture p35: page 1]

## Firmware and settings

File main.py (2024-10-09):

import sys

from micropython import const

import asyncio
import aioble
import bluetooth
import machine
import random
import struct
from machine import Pin, PWM

def uid():
    """ Return the unique id of the device as a string """
    return "{:02x}{:02x}{:02x}{:02x}{:02x}{:02x}{:02x}{:02x}".format(
        *machine.unique_id())


led = machine.Pin("LED", machine.Pin.OUT)
connection = None
connected = False


MANUFACTURER_ID = const(0x02A29)
MODEL_NUMBER_ID = const(0x2A24)
SERIAL_NUMBER_ID = const(0x2A25)
HARDWARE_REVISION_ID = const(0x2A26)
BLE_VERSION_ID = const(0x2A28)
_GENERIC = bluetooth.UUID(0x1848)
_BUTTON_UUID = bluetooth.UUID(0x2A6E)
# org.bluetooth.service.environmental_sensing
_ENV_SENSE_UUID = bluetooth.UUID(0x180A)
# org.bluetooth.characteristic.temperature
_ENV_SENSE_TEMP_UUID = bluetooth.UUID(0x2A6E)
# org.bluetooth.characteristic.gap.appearance.xml
_ADV_APPEARANCE_GENERIC_THERMOMETER = const(768)
_BLE_APPEARANCE_GENERIC_REMOTE_CONTROL = const(384)
# How frequently to send advertising beacons.
_ADV_INTERVAL_MS = 250_000

# Create characteristics for device info
device_info = aioble.Service(_ENV_SENSE_UUID)
aioble.Characteristic(device_info, bluetooth.UUID(MANUFACTURER_ID), read=True, initial="PicoRemote")
aioble.Characteristic(device_info, bluetooth.UUID(MODEL_NUMBER_ID), read=True, initial="1.0")
aioble.Characteristic(device_info, bluetooth.UUID(SERIAL_NUMBER_ID), read=True, initial=uid())
aioble.Characteristic(device_info, bluetooth.UUID(HARDWARE_REVISION_ID), read=True, initial=sys.version)
aioble.Characteristic(device_info, bluetooth.UUID(BLE_VERSION_ID), read=True, initial="1.0")

# Create characteristics and service of button class (we use this to send data from the bluetooth app)
remote_service = aioble.Service(_GENERIC)
button_characteristic = aioble.Characteristic(remote_service, _BUTTON_UUID, write=True, read=True, notify=True, capture=True)
aioble.register_services(remote_service, device_info)

# Check if GP15 pin is HIGH. If this pin is high, we are in servo control mode, and we don't do motor turning.
steering_mode = "motor"

pin_mode = Pin(15, Pin.IN)
# Read the pin state
pin_mode_state = pin_mode.value()

# Check if pin is high or low
if pin_mode_state == 1:
    steering_mode = "servo"

# Register all 4 pins that we need to control the motor controller (s)
pin_A_1 = PWM(Pin(0, mode=Pin.OUT))
pin_A_2 = PWM(Pin(1, mode=Pin.OUT))
pin_B_1 = PWM(Pin(2, mode=Pin.OUT))
pin_B_2 = PWM(Pin(3, mode=Pin.OUT))

# Register pin for the servo
pin_servo = PWM(Pin(6, mode=Pin.OUT))

# Set PWM frequency

pin_A_1.freq(50000)
pin_A_2.freq(50000)
pin_B_1.freq(50000)
pin_B_2.freq(50000)

# Set PWM frequency for servo
PWM_FREQUENCY = 50
pin_servo.freq(PWM_FREQUENCY)

# This would be periodically polling a hardware sensor.
async def sensor_task():
    global connected
    while True:
        if connected:
            char_obj = await button_characteristic.written()
            if char_obj != None:
                # Decode our input value from the joystick from a byte string to a regular string, then split it at our chosen split character (|)
                direction_tup = char_obj[1].decode().split("|")
                # Convert each of our values, angle and strength, to integers
                angle = int(direction_tup[0])
                strength = int(direction_tup[1]) 

                control_motors(angle, strength)

            else:
                print("Received none")
        await asyncio.sleep_ms(100)

# Main control function
def control_motors(angle, strength):
    # Pico PWM duty cycle is between 0-65025, where as our input from the joystick is 0-100, so we rescale it here.
    strength_duty = strength * 650 

    # Normalize angle to range between 0 to 360
    angle = angle % 360

    if steering_mode == "motor":
        if angle <= 90:  # First quadrant (forward, left turn)
            left_speed = strength_duty * (angle / 90)    # Increase left motor speed
            right_speed = strength_duty                  # Full speed on right motor

        elif angle <= 180:  # Second quadrant (forward, right turn)
            left_speed = strength_duty                   # Full speed on left motor
            right_speed = strength_duty * (1 - (angle - 90) / 90)  # Decrease right motor speed

        elif angle <= 270:  # Third quadrant (backward, right turn)
            left_speed = -strength_duty                  # Full reverse on left motor
            right_speed = -strength_duty * ((angle - 180) / 90)     # Increase reverse speed on right motor

        else:  # Fourth quadrant (backward, left turn)
            left_speed = -strength_duty * (1 - (angle - 270) / 90)  # Decrease reverse speed on left motor
            right_speed = -strength_duty                             # Full reverse on right motor

        # Apply motor speeds
        set_motor_speeds(left_speed, right_speed)

    else:
        if angle <= 180: # Top half (forward, angle)
            left_speed = strength_duty
            right_speed = strength_duty
            if(strength > 20): # Add this small limit in near the center to prevent lots of glitching near the middle
                set_servo_angle(180 - angle)
        else:
            left_speed = -strength_duty
            right_speed = -strength_duty
            if(strength > 20): # Add this small limit in near the center to prevent lots of glitching near the middle
                set_servo_angle((angle % 180))

        set_motor_speeds(left_speed, right_speed)



# Function to set motor speeds
def set_motor_speeds(left_speed, right_speed):

    # Left motor
    if left_speed >= 0:
        pin_A_1.duty_u16(int(left_speed))  # Forward
        pin_A_2.duty_u16(0)                # Reverse off
    else:
        pin_A_1.duty_u16(0)                # Forward off
        pin_A_2.duty_u16(int(-left_speed)) # Reverse

    # Right motor
    if right_speed >= 0:
        pin_B_1.duty_u16(int(right_speed)) # Forward
        pin_B_2.duty_u16(0)                # Reverse off
    else:
        pin_B_1.duty_u16(0)                # Forward off
        pin_B_2.duty_u16(int(-right_speed))# Reverse

def set_servo_angle(value, input_min=0, input_max=180, output_min=1000000, output_max=2000000):
    # Scaling formula
    scaled_value = int(((value - input_min) / (input_max - input_min)) * (output_max - output_min) + output_min)

    pin_servo.duty_ns(scaled_value)

# Serially wait for connections. Don't advertise while a central is connected.
async def peripheral_task():
    global connected, connection
    while True:
        async with await aioble.advertise(
            _ADV_INTERVAL_MS,
            name="robot-1",
            services=[_ENV_SENSE_UUID],
            appearance=_BLE_APPEARANCE_GENERIC_REMOTE_CONTROL,
        ) as connection:
            connected = True
            # print("Connection from", connection.device)
            await connection.disconnected(timeout_ms=None)
            connected = False

async def blink_task():
    toggle = True
    while True:
        led.value(toggle)
        toggle = not toggle
        blink = 1000
        if connected:
            blink = 1000
        else:
            blink = 250
        await asyncio.sleep_ms(blink)

# Run the three tasks.
async def main():
    tasks = [
        asyncio.create_task(peripheral_task()),
        asyncio.create_task(blink_task()),
        asyncio.create_task(sensor_task()),
    ]
    await asyncio.gather(*tasks)

asyncio.run(main())

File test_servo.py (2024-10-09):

import machine
from machine import Pin,PWM
import utime
def scale_value(value, input_min=0, input_max=180, output_min=1000000, output_max=2000000):
    # Scaling formula
    scaled_value = int(((value - input_min) / (input_max - input_min)) * (output_max - output_min) + output_min)

    return scaled_value


pwm = PWM(Pin(6))

pwm.freq(50)
pwm.duty_ns(scale_value(0))

while True:
    pwm.duty_ns(scale_value(0))
    utime.sleep(1)
    pwm.duty_ns(scale_value(90))
    utime.sleep(1)
    pwm.duty_ns(scale_value(180))
    utime.sleep(1)

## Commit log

2024-10-30 Add laser cuttable file
2024-10-30 Add 3D printable files
    [PicoBot-DrifterWheel.stl, PicoBot-Pivot-Mount.stl]
2024-11-23 Add battery instructions
